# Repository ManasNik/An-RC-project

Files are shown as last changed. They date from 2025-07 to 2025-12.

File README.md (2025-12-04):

# **An RC car project**
This is a work in progress personal project that I started with a goal of building an RC car from scratch with an IMU based steering controller imitating real life steering action and to gain experience with STM32 microcontrollers. My initial goal for this project is to complete the basic functioning of the car and steering control. I have planned and I am planning to add more features in the future such as controls to adjust certain parameters to affect the handling of the car, telemetry, lap time counter and even a camera to get a First Person View(FPV)!

# **Current status**
WhatsApp Image 2025-12-03 at 16 24 01_00abe4af

Hardware:
- The car prototype is almost complete. I designed a simple prototype PCB to mount the off-the-shelf modules that I previously tested on the breadboard. The layout is intentionally minimal to reduce cost, keep complexity low, and allow the modules to be reused in future projects.
- Added extra capacitors on the PCB to suppress electrical noise generated by the motors on the power rails.
- The car is powered by a 600 mAh 25C LiPo battery.
- The controller circuit is still under development on the breadboard. I’m currently testing different features, tuning behavior, and iterating on the design.

Software:
- Developed a NRF24L01 driver for wireless communication between the controller and the car.
- Developed a driver for the MPU6050 IMU. Using a complementary filter to combine accelerometer and gyroscope data for accurate steering-angle estimation.
- Implemented the core firmware for basic motion control (forward, reverse, left, right).

# **Development journey**
The following section documents my project journey in detail from the start to the current stage.

## **Components used(so far)**
TB6612FNG x2   
STM32F103CBT6 x2  
Potentiometers for intial testing x2  
NRF24L01 x2
MPU6050 x1

## **The initial breadboard circuit**
Initial Prototype
(It's a mess of wires!)

I started my project by testing individual motors with the driver and eventually wired them all together. I initially tested using the STM32F446RE Nucleo board since it was readily available with me then. Obviously it's an overkill for this project and so I decided to use the STM32F103CBT6, which is still a powerful MCU for this project but leaves me headroom for adding interesting features later on in the future.
I used two potentiometers - one for speed control(throttle) and the other for steering control. This is the point I learned about DMA(Direct Memory Access) as it was needed to process the two ADC channels efficiently. Additionally I used the built-in button on the Nucleo board to enable/disable reverse under a specified speed. My idea is to implement the reverse button on the steering wheel controller later on in the future to engage/disengage reverse like in an F1 car! It has to be noted that the controller is not designed or involved in this initial setup - This is a hardwired test. 

I wanted to design a simple platform to hold my motors (the chassis) and small wheels to fit my desired form factor. I decided to design and 3D print my own design.

**Chassis design**
Chassis design

**Wheel design**
Wheel design

**The outcome of the design**
Finished model parts
(Placed a mouse there for comparison!)

# **Implementing remote control**
Circuit with wireless control  
(The car circuit is on the left and the controller on the right)

In this stage of the project I decided to add the remote control using two NRF24L01 modules - one on the car and one in the controller. To develop the driver for communicating with this module, I followed a YouTube tutorial and the NRF24l01 datasheet. This is the first time I wrote a driver by manipulating low level registers -  a great learning experience indeed! Once the driver development was done, it was time to test it. I shifted the two potentiometers and the reverse button to one of the two STM32F103CBT6 boards I will be using for the rest of this project and connected the NRF24L01 module via SPI. Similarly, I shifted the motor drivers to the other STM32F103CBT6 board and connected the other NRF24L01 module via SPI. I was now able to control the car through wireless communication!

# **Implementing IMU based steering control**
I chose the cheap and easily available MPU6050 Inertial Measurement Unit(IMU) module and developed a driver to communicate with it using I2C. After I confirmed I was receiving the gyroscope and accelerometer data from the IMU, I started working on the code to process it. I used a simple Exponential Moving Average (EMA) filter to smoothen out some noise from the readings, and used a complementary filter to combine the readings of both the gyroscope and the accelerometer to improve the steering angle estimation. 

I scaled the steering angle estimation and computed a steering amount to add or subtract from the PWM control values to change the motor speeds according to the direction of the steering. The car doesn't have a deciated mechanical steering system and the steering rotation is achieved by varying the speeds on each side of the car. To turn left, the speed is reduced on the left side and increased on the right side and vice versa.

# **PCB Design** 
I designed a simple 2-layered PCB to transfer the breadboard circuit onto the 3d printed car platform I previously designed. I can now test the car on the ground with the control logic I developed in software and fine tune it to improve the handling characteristics. I intentionally made the PCB design simple by using footprints for female/socket headers spaced appropriately to insert the off-the-shelf modules. This reduced the complexity of the design, made it cheaper to manufacture and made it possible to resue the modules for other projects. 

**Schematic**
RC car schematic_page-0001

**PCB design**



Final PCB
WhatsApp Image 2025-12-03 at 16 24 01_501648d1

This was my first time designing a PCB on my own and ordering it. Obviously I made mistakes!
- I forgot to include capacitors in the design to reduce the noise on the power lines, since the brushed DC motors cause electrical noise due to brush-commutator sparking. This noise interfered a lot with the NRF24L01 module making it lose connection with the controller. I greatly reduced this later by soldering electrolytic and ceramic capacitors near the motor termianls and power supply pins of the modules.
- I should've taken extra care to provide a stable power supply directly to the NRF24L01 module instead of supplying it from the 3.3V pin of the STM32 module.
 
# **What's next?**
(This section will be updated from time to time till the completion of the project)
- The car is pretty quick on the ground and coasts to a stop instead of stopping quickly. I am working on a braking logic to slow down the car on command. The brake paddle will be one of the two paddles I'm planning to add behind my steering wheel controller with the other one being the throttle paddle. I will develop the logic in such a way that the user can fine tune the characteristics of the car according to their preference.
- I'm planning to add a Time-Of-Flight sensor at the front of the car to detect obstacles ahead to avoid a head-on collision when the controller connection is lost - A backup safety feature.
- I will develop a simple pit limiter making use of a hall sensor to measure wheel RPM to enable closed loop speed control. The hall sensor will also be crucial to avoid unwanted movement of the car due to steering movement even when no throttle is applied at rest.

This project for me isn't just about building an RC car - it's a fun learning experience that will help me dive deep into complete embedded system design from the ground up.

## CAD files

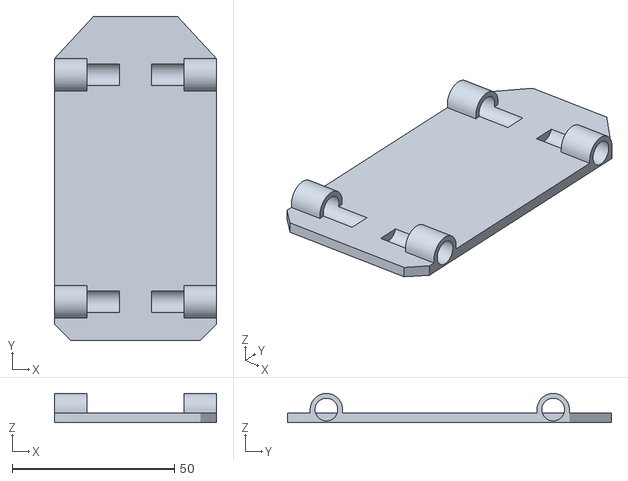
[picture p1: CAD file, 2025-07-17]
Model design/Testing model/chassis.stl
50.0 x 100.0 x 9.00

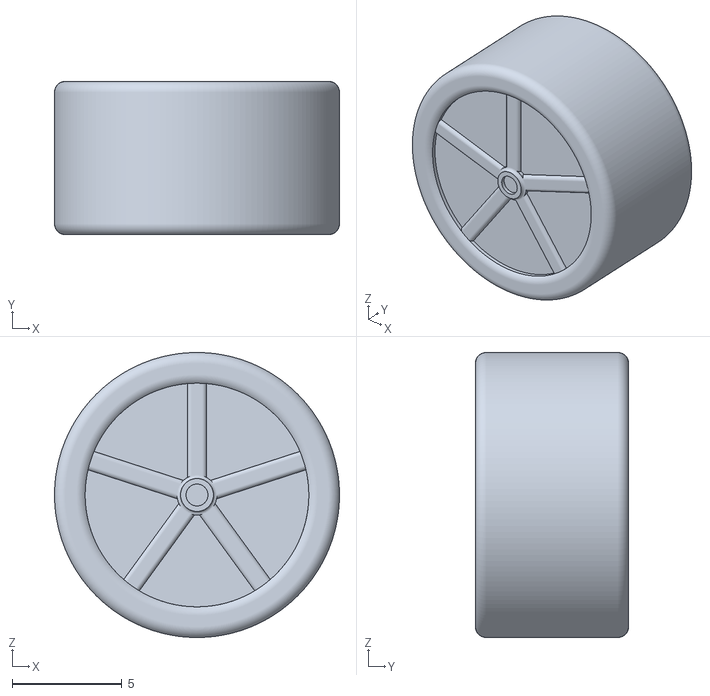
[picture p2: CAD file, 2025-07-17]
Model design/Testing model/Wheel.stl
13.0 x 7.00 x 13.0

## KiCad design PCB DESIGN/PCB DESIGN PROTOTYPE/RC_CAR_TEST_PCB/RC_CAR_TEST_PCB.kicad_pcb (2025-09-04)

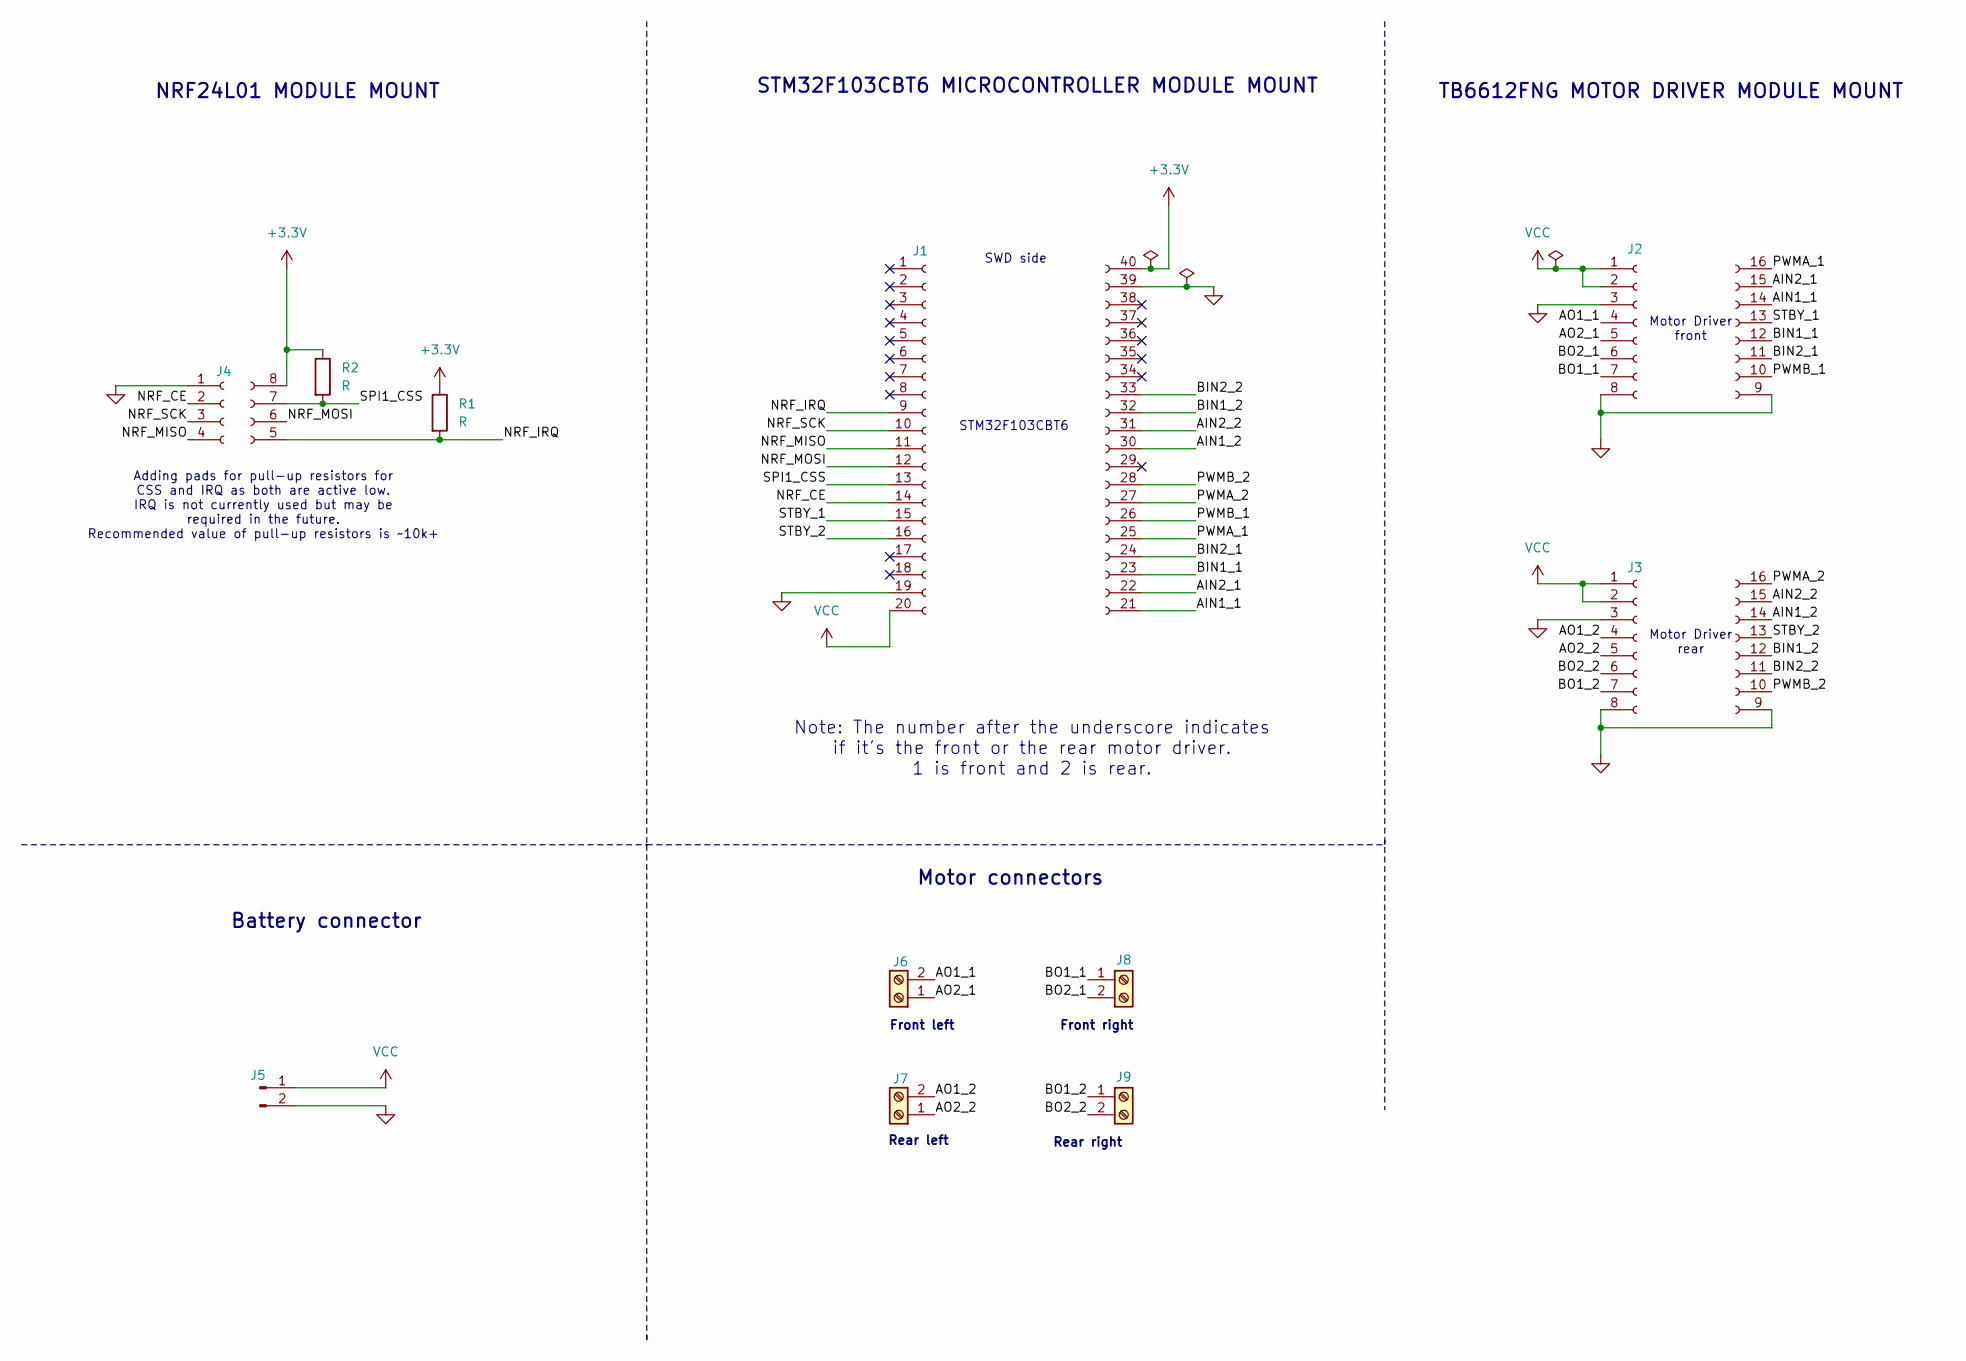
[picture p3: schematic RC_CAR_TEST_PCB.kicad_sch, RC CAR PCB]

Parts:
J1: Conn_02x20_Socket; Bluepill
J2, J3: Conn_02x08_Socket; TB6612FNG
J4: Conn_01x04_Socket; NRF24L01
J5: Conn_01x02_Pin; JST_VH_B2P-VH_1x02_P3.96mm_Vertical
J6, J7, J8, J9: Screw_Terminal_01x02; TerminalBlock_4Ucon_1x02_P3.50mm_Horizontal
R1, R2: R; R_Axial_DIN0204_L3.6mm_D1.6mm_P5.08mm_Horizontal

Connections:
+3.3V: J1.40 (Pin_20), J4.8 (Pin_4), R1.1, R2.1
/AIN1_1: J1.21 (Pin_1), J2.14 (Pin_3)
/AIN1_2: J1.30 (Pin_10), J3.14 (Pin_3)
/AIN2_1: J1.22 (Pin_2), J2.15 (Pin_2)
/AIN2_2: J1.31 (Pin_11), J3.15 (Pin_2)
/AO1_1: J2.4, J6.2
/AO1_2: J3.4, J7.2
/AO2_1: J2.5, J6.1
/AO2_2: J3.5, J7.1
/BIN1_1: J1.23 (Pin_3), J2.12 (Pin_5)
/BIN1_2: J1.32 (Pin_12), J3.12 (Pin_5)
/BIN2_1: J1.24 (Pin_4), J2.11 (Pin_6)
/BIN2_2: J1.33 (Pin_13), J3.11 (Pin_6)
/BO1_1: J2.7, J8.1
/BO1_2: J3.7, J9.1
/BO2_1: J2.6, J8.2
/BO2_2: J3.6, J9.2
/NRF_CE: J1.14, J4.2
/NRF_IRQ: J1.9, J4.5 (Pin_1), R1.2
/NRF_MISO: J1.11, J4.4
/NRF_MOSI: J1.12, J4.6 (Pin_2)
/NRF_SCK: J1.10, J4.3
/PWMA_1: J1.25 (Pin_5), J2.16 (Pin_1)
/PWMA_2: J1.27 (Pin_7), J3.16 (Pin_1)
/PWMB_1: J1.26 (Pin_6), J2.10 (Pin_7)
/PWMB_2: J1.28 (Pin_8), J3.10 (Pin_7)
/SPI1_CSS: J1.13, J4.7 (Pin_3), R2.2
/STBY_1: J1.15, J2.13 (Pin_4)
/STBY_2: J1.16, J3.13 (Pin_4)
GND: J1.19, J1.39 (Pin_19), J2.3, J2.8, J2.9 (Pin_8), J3.3, J3.8, J3.9 (Pin_8), J4.1, J5.2
VCC: J1.20, J2.1, J2.2, J3.1, J3.2, J5.1

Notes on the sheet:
Front left
STM32F103CBT6
TB6612FNG MOTOR DRIVER MODULE MOUNT
Motor connectors
Adding pads for pull-up resistors for CSS and IRQ as both are active low. IRQ is not currently used but may be required in the future. Recommended value of pull-up resistors is ~10k+
Front right
Note: The number after the underscore indicates if it's the front or the rear motor driver. 1 is front and 2 is rear.
Rear left
Rear right
NRF24L01 MODULE MOUNT
Motor Driver front
SWD side
STM32F103CBT6 MICROCONTROLLER MODULE MOUNT
Motor Driver rear
Battery connector

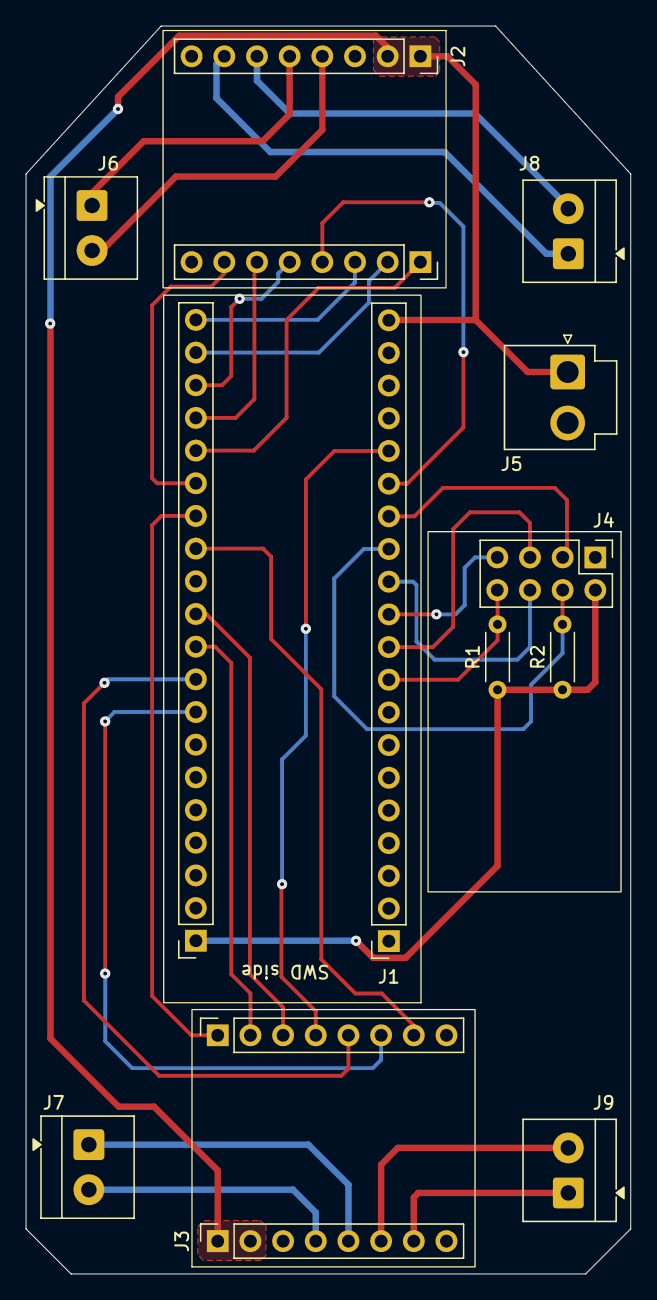
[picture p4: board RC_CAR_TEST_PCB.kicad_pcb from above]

Board: 2 copper layers, 47.0 x 97.0 mm, 11 parts (0 on the bottom side), 31 nets.

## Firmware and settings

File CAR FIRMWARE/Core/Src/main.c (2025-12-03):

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
/* Includes ------------------------------------------------------------------*/
#include "main.h"

/* USER CODE BEGIN Includes */
#include "stdbool.h"
#include "TB6612FNG.h"
#include "NRF24L01.h"
#include "stdlib.h"
/* USER CODE END Includes */

SPI_HandleTypeDef hspi1;

TIM_HandleTypeDef htim1;

/* USER CODE BEGIN PV */
tb6612fng_t motor_driver; // Custom struct for all motor driver pins and PWM channels

uint16_t throttle;
int16_t steering;

bool in1 = true; // CW or forward by default
bool in2 = false;

uint8_t RX_address[] = {0xEE,0xDD,0xCC,0xBB,0xAA};
uint8_t RX_buffer[5];

/* USER CODE END PV */

void SystemClock_Config(void);
static void MX_GPIO_Init(void);
static void MX_SPI1_Init(void);
static void MX_TIM1_Init(void);
/* USER CODE BEGIN PFP */
void tb6612fng_config(tb6612fng_t* tbf);
/* USER CODE END PFP */

/**
  * @brief  The application entry point.
  * @retval int
  */
int main(void)
{

  /* MCU Configuration--------------------------------------------------------*/

  /* Reset of all peripherals, Initializes the Flash interface and the Systick. */
  HAL_Init();

  /* Configure the system clock */
  SystemClock_Config();

  /* Initialize all configured peripherals */
  MX_GPIO_Init();
  MX_SPI1_Init();
  MX_TIM1_Init();
  /* USER CODE BEGIN 2 */
  tb6612fng_config(&motor_driver); // Assign values to struct attributes
  tb6612fng_init(&motor_driver);

  nrf24_init();
  nrf24_RXmode(RX_address, 5, 10);
  /* USER CODE END 2 */

  /* Infinite loop */
  /* USER CODE BEGIN WHILE */
  while (1)
  {
	  if(isDataAvailable(1)){
		  nrf24_Receive(RX_buffer,5);
		  HAL_GPIO_TogglePin(LED_GPIO_Port, LED_Pin);
	  }

	  // Note: Data in RX_buffer follows the same indexing as TX data buffer.
	  if((bool)RX_buffer[0] == 0){
		  in1 = false;
		  in2 = true;
	  }
	  else{
		  in1 = true;
		  in2 = false;
	  }

	  // Reconstruction of the 16-bit speed values from the two received 8-bit data pairs.
	  throttle = ((uint16_t) RX_buffer[1] << 8) | RX_buffer[2];
	  steering = ((int16_t) RX_buffer[3] << 8) | RX_buffer[4];

	  uint16_t speed_left = throttle + steering;
	  uint16_t speed_right = throttle - steering;

	  // Forward or reverse control
	  tb6612fng_direction(&motor_driver, in1, in2);

	  // Control the speed and steering
	  tb6612fng_speed(motor_driver, speed_left, speed_right);
    /* USER CODE END WHILE */

    /* USER CODE BEGIN 3 */
  }
  /* USER CODE END 3 */
}

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
/* USER CODE BEGIN 4 */
// Instance of the motor driver struct
	void tb6612fng_config(tb6612fng_t* tbf){

		// Number after the underscore represents the front(1)/rear(2) motor driver.
		tbf->stdby_front_port = STBY_1_GPIO_Port;
		tbf->stdby_front_pin = STBY_1_Pin;

		tbf->stdby_rear_port = STBY_2_GPIO_Port;
		tbf->stdby_rear_pin = STBY_2_Pin;

		// Front left
		tbf->AIN1_front_port = AIN1_1_GPIO_Port;
		tbf->AIN1_front_pin = AIN1_1_Pin;

		tbf->AIN2_front_port = AIN2_1_GPIO_Port;
		tbf->AIN2_front_pin = AIN2_1_Pin;

		// Front right
		tbf->BIN1_front_port = BIN1_1_GPIO_Port;
		tbf->BIN1_front_pin = BIN1_1_Pin;

		tbf->BIN2_front_port = BIN2_1_GPIO_Port;
		tbf->BIN2_front_pin = BIN2_1_Pin;

		// Rear left
		tbf->AIN1_rear_port = AIN1_2_GPIO_Port;
		tbf->AIN1_rear_pin = AIN1_2_Pin;

		tbf->AIN2_rear_port = AIN2_2_GPIO_Port;
		tbf->AIN2_rear_pin = AIN2_2_Pin;

		// Rear right
		tbf->BIN1_rear_port = BIN1_2_GPIO_Port;
		tbf->BIN1_rear_pin = BIN1_2_Pin;

		tbf->BIN2_rear_port = BIN2_2_GPIO_Port;
		tbf->BIN2_rear_pin = BIN2_2_Pin;

		tbf->htim = &htim1;

		tbf->front_left = TIM_CHANNEL_1;
		tbf->front_right = TIM_CHANNEL_2;
		tbf->rear_left = TIM_CHANNEL_3;
		tbf->rear_right = TIM_CHANNEL_4;

	}
/* USER CODE END 4 */
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


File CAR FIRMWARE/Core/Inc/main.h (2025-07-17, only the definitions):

#define CSS_Pin GPIO_PIN_0
#define CSS_GPIO_Port GPIOB
#define CE_Pin GPIO_PIN_1
#define CE_GPIO_Port GPIOB
#define LED_Pin GPIO_PIN_2
#define LED_GPIO_Port GPIOB
#define STBY_1_Pin GPIO_PIN_10
#define STBY_1_GPIO_Port GPIOB
#define STBY_2_Pin GPIO_PIN_11
#define STBY_2_GPIO_Port GPIOB
#define AIN1_1_Pin GPIO_PIN_12
#define AIN1_1_GPIO_Port GPIOB
#define AIN2_1_Pin GPIO_PIN_13
#define AIN2_1_GPIO_Port GPIOB
#define BIN1_1_Pin GPIO_PIN_14
#define BIN1_1_GPIO_Port GPIOB
#define BIN2_1_Pin GPIO_PIN_15
#define BIN2_1_GPIO_Port GPIOB
#define PWMA_1_Pin GPIO_PIN_8
#define PWMA_1_GPIO_Port GPIOA
#define PWMB_1_Pin GPIO_PIN_9
#define PWMB_1_GPIO_Port GPIOA
#define PWMA_2_Pin GPIO_PIN_10
#define PWMA_2_GPIO_Port GPIOA
#define PWMB_2_Pin GPIO_PIN_11
#define PWMB_2_GPIO_Port GPIOA
#define AIN1_2_Pin GPIO_PIN_15
#define AIN1_2_GPIO_Port GPIOA
#define AIN2_2_Pin GPIO_PIN_3
#define AIN2_2_GPIO_Port GPIOB
#define BIN1_2_Pin GPIO_PIN_4
#define BIN1_2_GPIO_Port GPIOB
#define BIN2_2_Pin GPIO_PIN_5
#define BIN2_2_GPIO_Port GPIOB

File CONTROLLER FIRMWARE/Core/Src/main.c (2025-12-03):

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
/* Includes ------------------------------------------------------------------*/
#include "main.h"

/* USER CODE BEGIN Includes */
#include "stdbool.h"
#include "math.h"
#include "NRF24L01.h"
#include "MPU6050.h"
#include "Pedals.h"
#include "EMA.h"
/* USER CODE END Includes */

/* USER CODE BEGIN PD */
#define SAMPLE_TIME_MS 20
#define COMP_FLT_ALPHA 0.4f
/* USER CODE END PD */

ADC_HandleTypeDef hadc1;
DMA_HandleTypeDef hdma_adc1;

I2C_HandleTypeDef hi2c1;

SPI_HandleTypeDef hspi1;

TIM_HandleTypeDef htim3;

/* USER CODE BEGIN PV */
// Transmitter variables
uint8_t TX_address[] = {0xEE,0xDD,0xCC,0xBB,0xAA};
uint8_t TX_data[5];

// ADC input variables for throttle and braking inputs
uint16_t adc_val[2];
uint16_t throttle;

// Brake input
uint16_t brake_input;
// Brake amount
uint8_t braking;

// Acceleration and deceleration(motor braking - slowing down motor using PWM)
uint8_t accel = 3;
uint8_t decel = 3;

// Steering variables
float steering_gain = 1.0f; // Ranges from 1 to 0. Decreases as speed increases. High gain means more steering.
int16_t steering; // Actual steering amount

// Final speeds
uint16_t speed_left;
uint16_t speed_right;

bool direction = true; // Forward(true) or backward(false)

/* Accelerometer variables
 * We only need x and y to calculate roll along z-axis. Note that here roll is calculated
 * around z-axis since the device is hand held such that we face the z-axis.
 * Gyroscope readings will also be used later along with accelerometer readings to make the
 * roll angle calculation more accurate.
 */
float ax,ay,gz;
float roll_est;

float roll_angle_z; // The calculated angle around Z-axis
float steering_angle = 0.0f; // Determines the steering

EMA_t ema_ax, ema_ay, ema_gz;
float filter_ax, filter_ay, filter_gz;

uint32_t lastSampled = 0;
// Test variable
int dir = 1;
/* USER CODE END PV */

void SystemClock_Config(void);
static void MX_GPIO_Init(void);
static void MX_DMA_Init(void);
static void MX_ADC1_Init(void);
static void MX_TIM3_Init(void);
static void MX_SPI1_Init(void);
static void MX_I2C1_Init(void);
/* USER CODE BEGIN PFP */
static inline
float map_range(float input, float input_start, float input_end, float output_start, float output_end);
/* USER CODE END PFP */

/**
  * @brief  The application entry point.
  * @retval int
  */
int main(void)
{

  /* MCU Configuration--------------------------------------------------------*/

  /* Reset of all peripherals, Initializes the Flash interface and the Systick. */
  HAL_Init();

  /* Configure the system clock */
  SystemClock_Config();

  /* Initialize all configured peripherals */
  MX_GPIO_Init();
  MX_DMA_Init();
  MX_ADC1_Init();
  MX_TIM3_Init();
  MX_SPI1_Init();
  MX_I2C1_Init();
  /* USER CODE BEGIN 2 */
  /* Initializing Exponential Moving Average filter with alpha 0.5 for cleaning
   * Accelerometer and Gyroscope outputs before giving as input to the complementary filter.
  */
  EMA_init(&ema_ax, 0.5);
  EMA_init(&ema_ay, 0.5);
  EMA_init(&ema_gz, 0.5);

  nrf24_init();
  nrf24_TXmode(TX_address, 10);

  HAL_ADC_Start_DMA(&hadc1, (uint32_t *) adc_val, 2);
  HAL_TIM_Base_Start(&htim3);

  // Create an instance of MPU6050 struct.
  MPU6050_t imu;
  /* USER CODE END 2 */

  /* Infinite loop */
  /* USER CODE BEGIN WHILE */
  while (1)
  {
	// Reverse enable/disable
	if(HAL_GPIO_ReadPin(REVERSE_GPIO_Port, REVERSE_Pin) == GPIO_PIN_SET){
	  if(throttle <= 100){
	  direction = !direction;
	  HAL_GPIO_TogglePin(REVERSE_GPIO_Port, REVERSE_Pin);
	  }
	}

	// Scale the ADC value to range 0 to 1000.
	throttle = (adc_val[0]*1000)/4096;

	MPU6050_Read_Accel(&imu);
	ax = imu.accel_x;
	ay = imu.accel_y;

	filter_ax = EMA_update(&ema_ax, ax);
	filter_ay = EMA_update(&ema_ay, ay);

	// Roll(Phi) estimate from accelerometer data(in radians)
	roll_est = atan2f(filter_ay,filter_ax);

	MPU6050_Read_Gyro(&imu);
	gz = imu.gyro_z;

	filter_gz = EMA_update(&ema_gz, gz) * (M_PI/180.0);

	/* Sensor fusion between accelerometer and gyroscope using complementary filter
	 * Angle_n+1 = Accl_n * alpha + (1-alpha)(angle_n + (dt*Gyr_n))
	 */

	// Compute dt
	uint32_t now = HAL_GetTick();
	float dt = (now - lastSampled) / 1000.0f;
	lastSampled = now;

	roll_angle_z = roll_est * COMP_FLT_ALPHA + (1 - COMP_FLT_ALPHA)*(roll_angle_z + dt *filter_gz);

	steering_angle = roll_angle_z * (180.0/M_PI);

	float steering_scaled = map_range(steering_angle, -120.0f, 120.0f, -200.0f, 200.0f);

	steering = steering_gain + steering_scaled;

	TX_data[0] = (uint8_t) direction;
	// Note: 16-bit values are sent as two 8-bit values with MSB stored in lower index than LSB.
	TX_data[1] = (throttle >> 8) & 0xFF;
	TX_data[2] = (throttle & 0xFF);
	TX_data[3] = (steering >> 8) & 0xFF;
	TX_data[4] = (steering & 0xFF);

	if(nrf24_Transmit(TX_data,5)){
		HAL_GPIO_TogglePin(TX_LED_GPIO_Port, TX_LED_Pin);
		HAL_Delay(100);
	}
    /* USER CODE END WHILE */

    /* USER CODE BEGIN 3 */
  }
  /* USER CODE END 3 */
}

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
/* USER CODE BEGIN 4 */
// Helper Functions
static inline float map_range(float input, float input_start, float input_end, float output_start, float output_end){
	return output_start + ((output_end - output_start) / (input_end - input_start)) * (input - input_start);
}
/* USER CODE END 4 */
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


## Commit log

2025-07-17 Inital commit: Car protoype design
    [Wheel.stl, chassis.stl]
2025-09-04 Developed MPU6050 driver and used the accelerometer values for steering
2025-09-04 Made my first PCB and the first for this project.
    [RC_CAR_TEST_PCB.kicad_pcb, RC_CAR_TEST_PCB.kicad_sch]
2025-12-03 Updates and progress
    [RC_CAR_TEST_PCB-B_Cu.gbr, RC_CAR_TEST_PCB-B_Mask.gbr, RC_CAR_TEST_PCB-B_Paste.gbr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]
2025-12-03 Update README with project status and future plans
    Expanded project details and current status, including hardware and software updates. Added sections on PCB design and future plans.
2025-12-04 Update README
    Added final PCB image and personal notes on design mistakes.

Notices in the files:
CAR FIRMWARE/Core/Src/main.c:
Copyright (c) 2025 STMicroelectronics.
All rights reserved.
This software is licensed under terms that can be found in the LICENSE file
